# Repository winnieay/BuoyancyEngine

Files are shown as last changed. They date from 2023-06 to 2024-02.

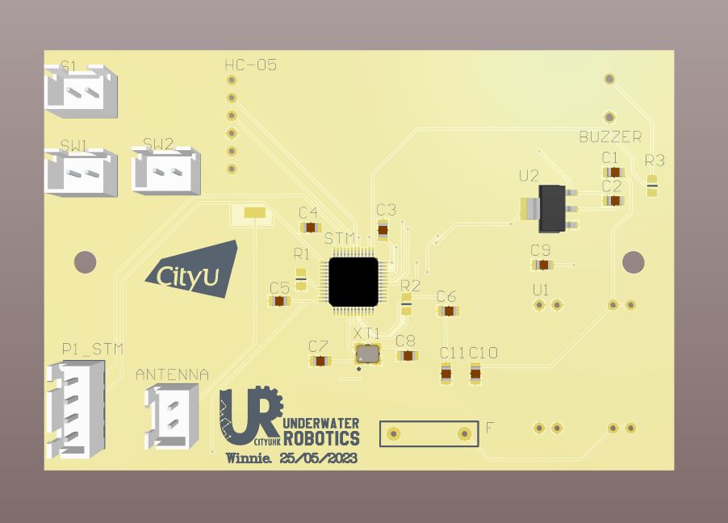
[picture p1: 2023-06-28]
BE_GroundReceiver_PCB/PCB_OUTPUT_3D.JPG

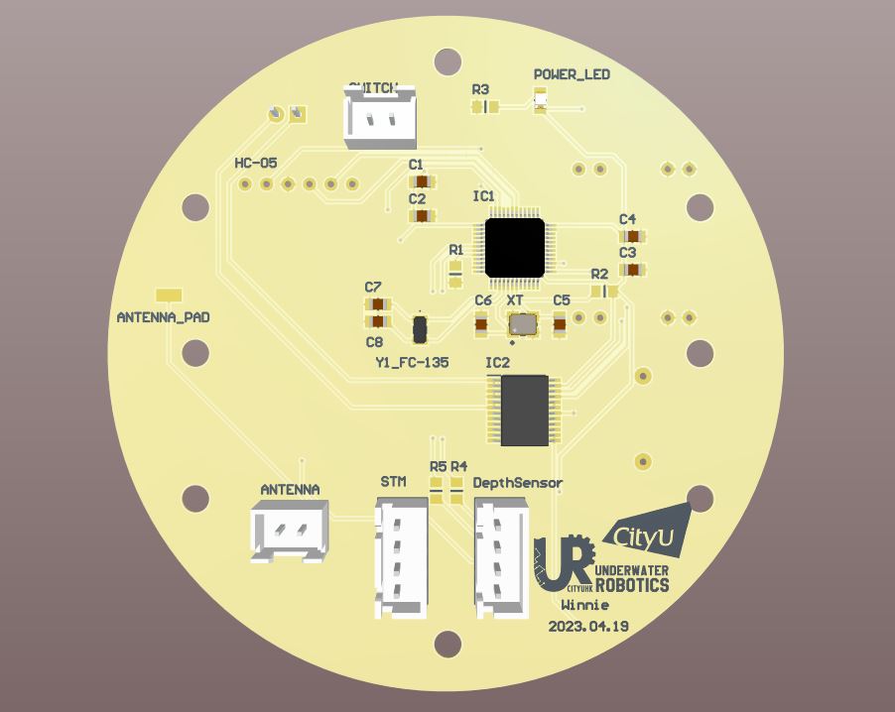
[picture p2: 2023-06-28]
BE_Engine_PCB/PCB_OUTPUT_3D.JPG

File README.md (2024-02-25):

# BuoyancyEngine

The buoyancy engine is built with two watertight enclosures and external mounting support. These two watertight enclosure kits are assembled by PMMA tubes and the aluminum alloy flanges. 

The upper part, the electrical enclosure, includes one 2.4GHz antenna, one customized PCB, one pressure sensor,one peristaltic pump, two 9V batteries and other electrical components. The enclosure on the bottom is mainly used for storing the water drived by the peristaltic pump.

<p align="center">
    <h3>Rendered Buoyancy Engine</h3> <br />
    
    <br />
</p>

<p align="center">
    <h3>Buoyancy Engine Working Example</h3> <br />
   <br />
</p>

<p align="center">
    <h3>PCB Design & Ground Receiver</h3> <br />
   <br />
</p>

<h2>Specification</h2>

1. Watertight Enclosure

+ Thickness: 5mm

+ Outer Dimension: 90mm

+ Length: (Upper)250mm, (Lower)100mm

2. Bouyancy Engine

+ Height: 620mm

+ Dimension: 120mm

<h2>Mechanism</h2>

As peristaltic pumps have no check valves to clog, they excel at driving fluids into lower pressure systems. Therefore, a peristaltic pump would be used to manipulate the motion of the engine: Sinking and Floating. Water is pumped through a flexible silicone tube in a peristaltic motion. Rollers are attached to a rotor that is controlled by a motor. As the rotor turns, the rollers pinch the tubing to force the water through. When the tube is not compressed, the water would be driven into the enclosure or pumped out the enclosure.

To indicate the position of the engine, a pressure sensor is one of the critical components in the engine. The engine could self-identify its position by taking advantage of the relationship between the fluid pressure and depth.

<h2>Data Transmission</h2>

For the communication between the ground station and the engine, a short-range wireless technology standard, Bluetooth, would be used to transmit and receive data. To avoid  improper connection, master-slave mode would be set up in the bluetooth modules. They are only allowed to be paired with each other and keep requiring re-pairing if they disconnect. A 2.4GHz antenna would increase signal strength to guarantee the data transmission even with long distance.

<h2>Buoyancy Support and Mounting Design</h2>

As the engine is positively buoyant, certain weights would be added into the lower enclosure to achieve slight positive buoyancy. Extra weights could be added or mounted to the 3D printed support with zip ties. It provides a flexible approach for buoyancy tuning while the engine is deployed into distinct environments.

To prevent electrical shock, the battery mount is designed to fix the position of the batteries onto the customized PCB. And the customized PCB would be mounting onto the upper aluminum alloy flange.

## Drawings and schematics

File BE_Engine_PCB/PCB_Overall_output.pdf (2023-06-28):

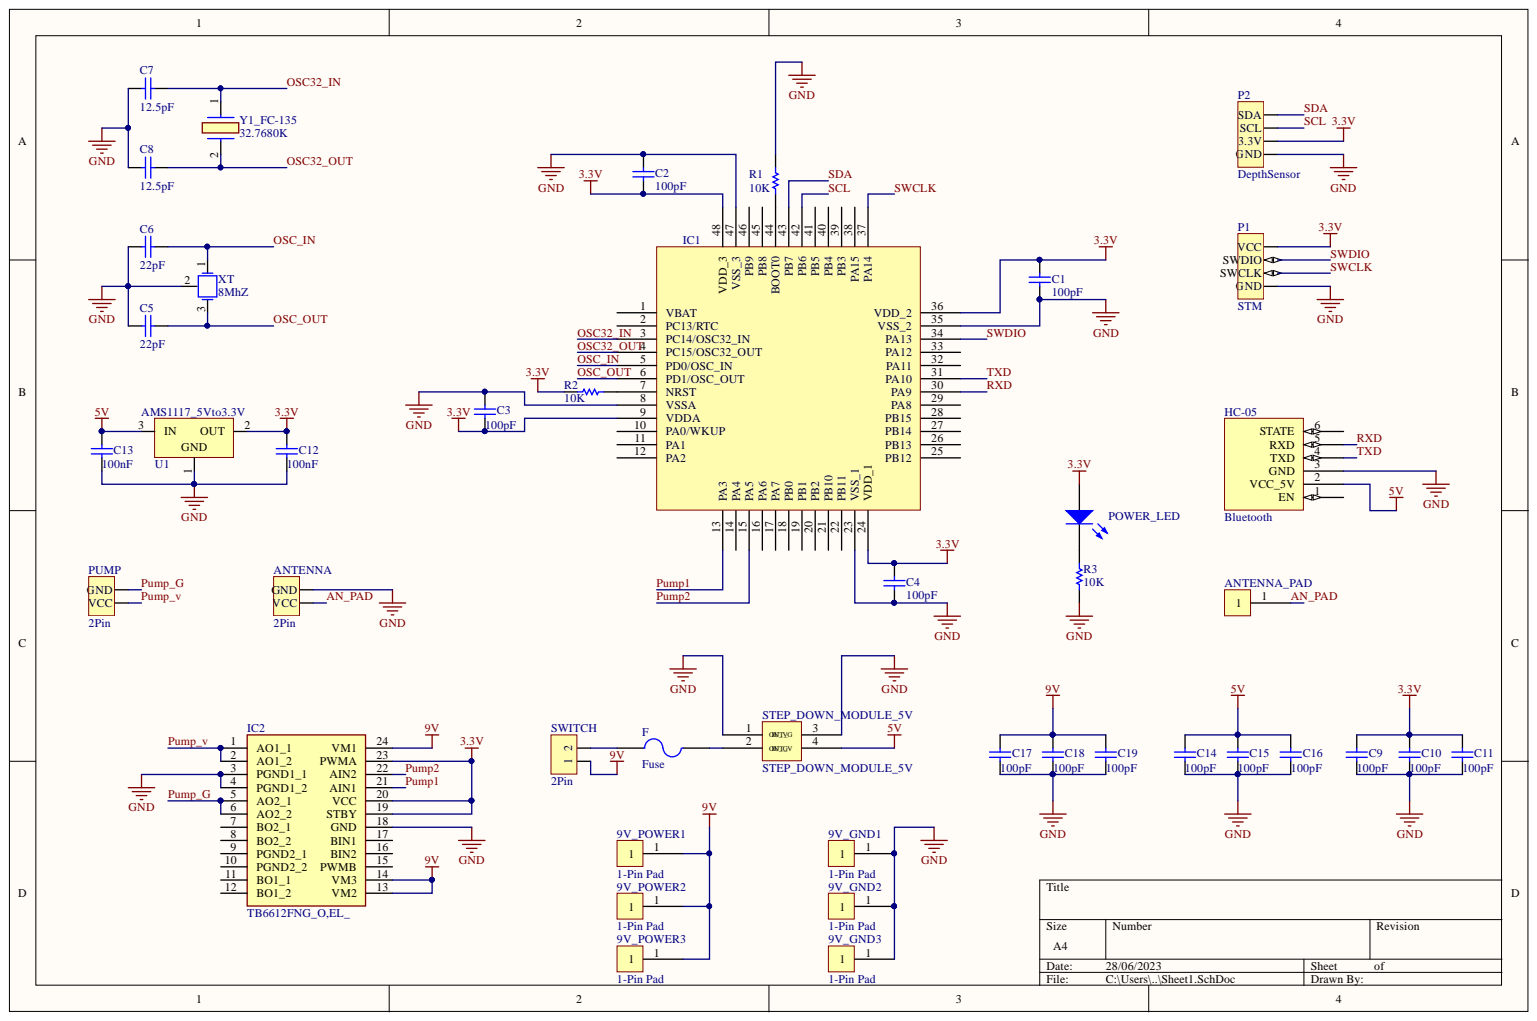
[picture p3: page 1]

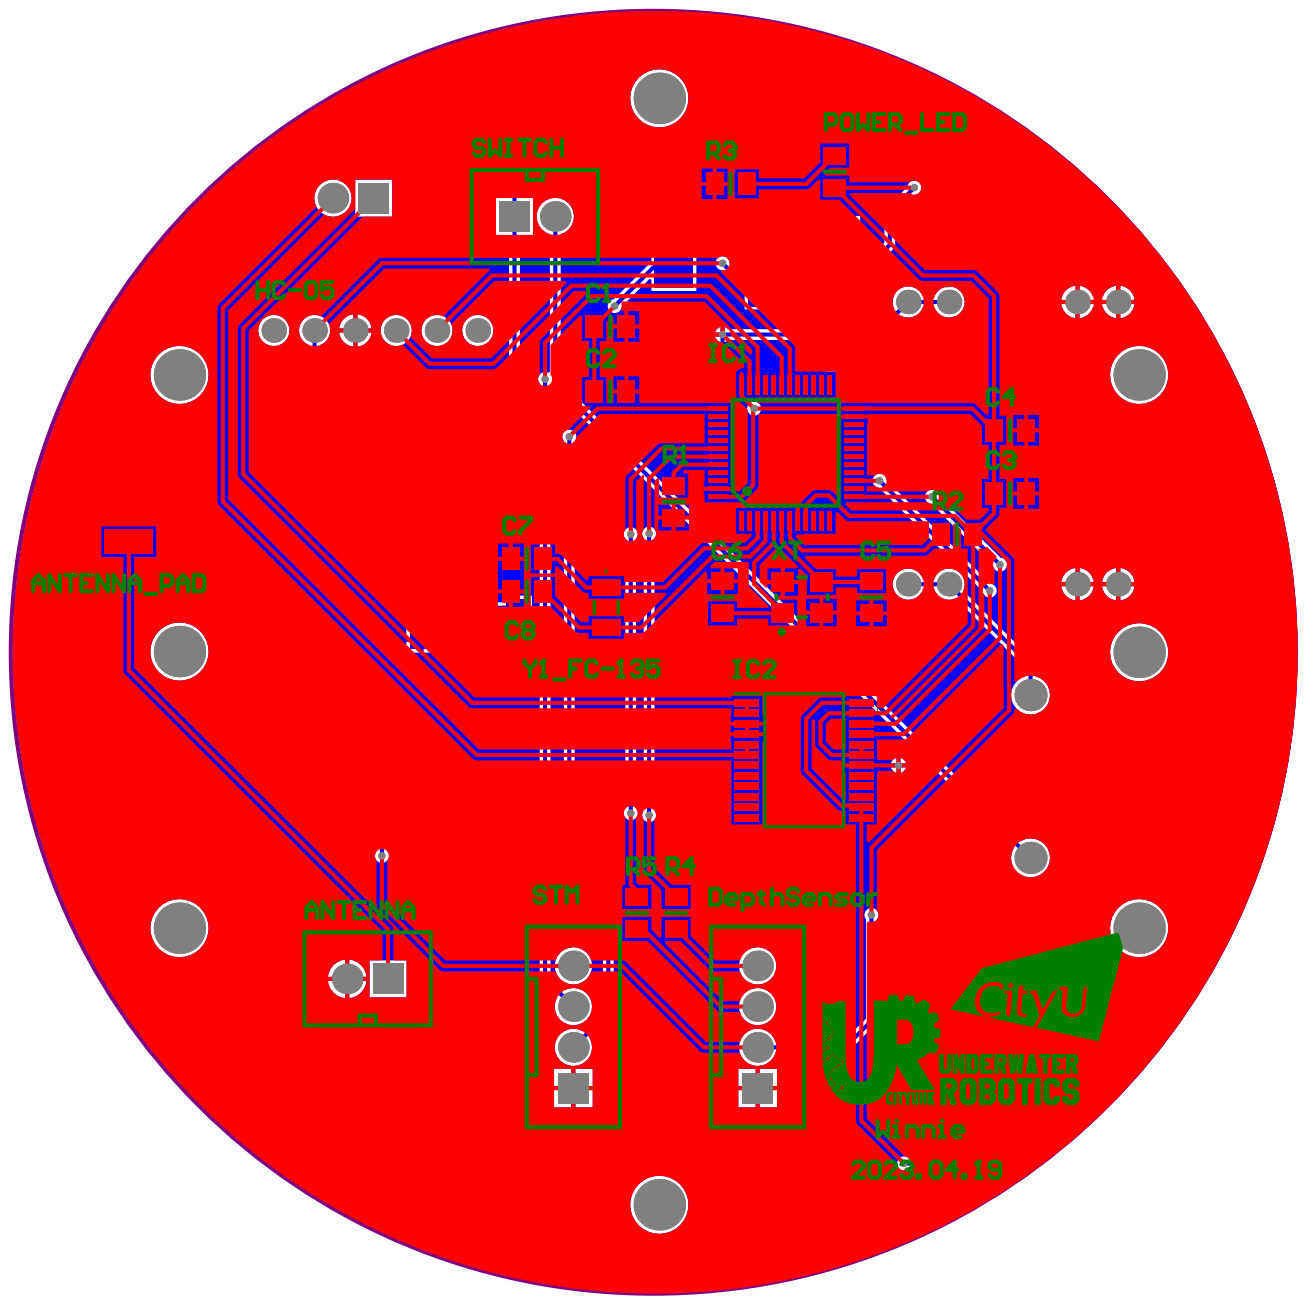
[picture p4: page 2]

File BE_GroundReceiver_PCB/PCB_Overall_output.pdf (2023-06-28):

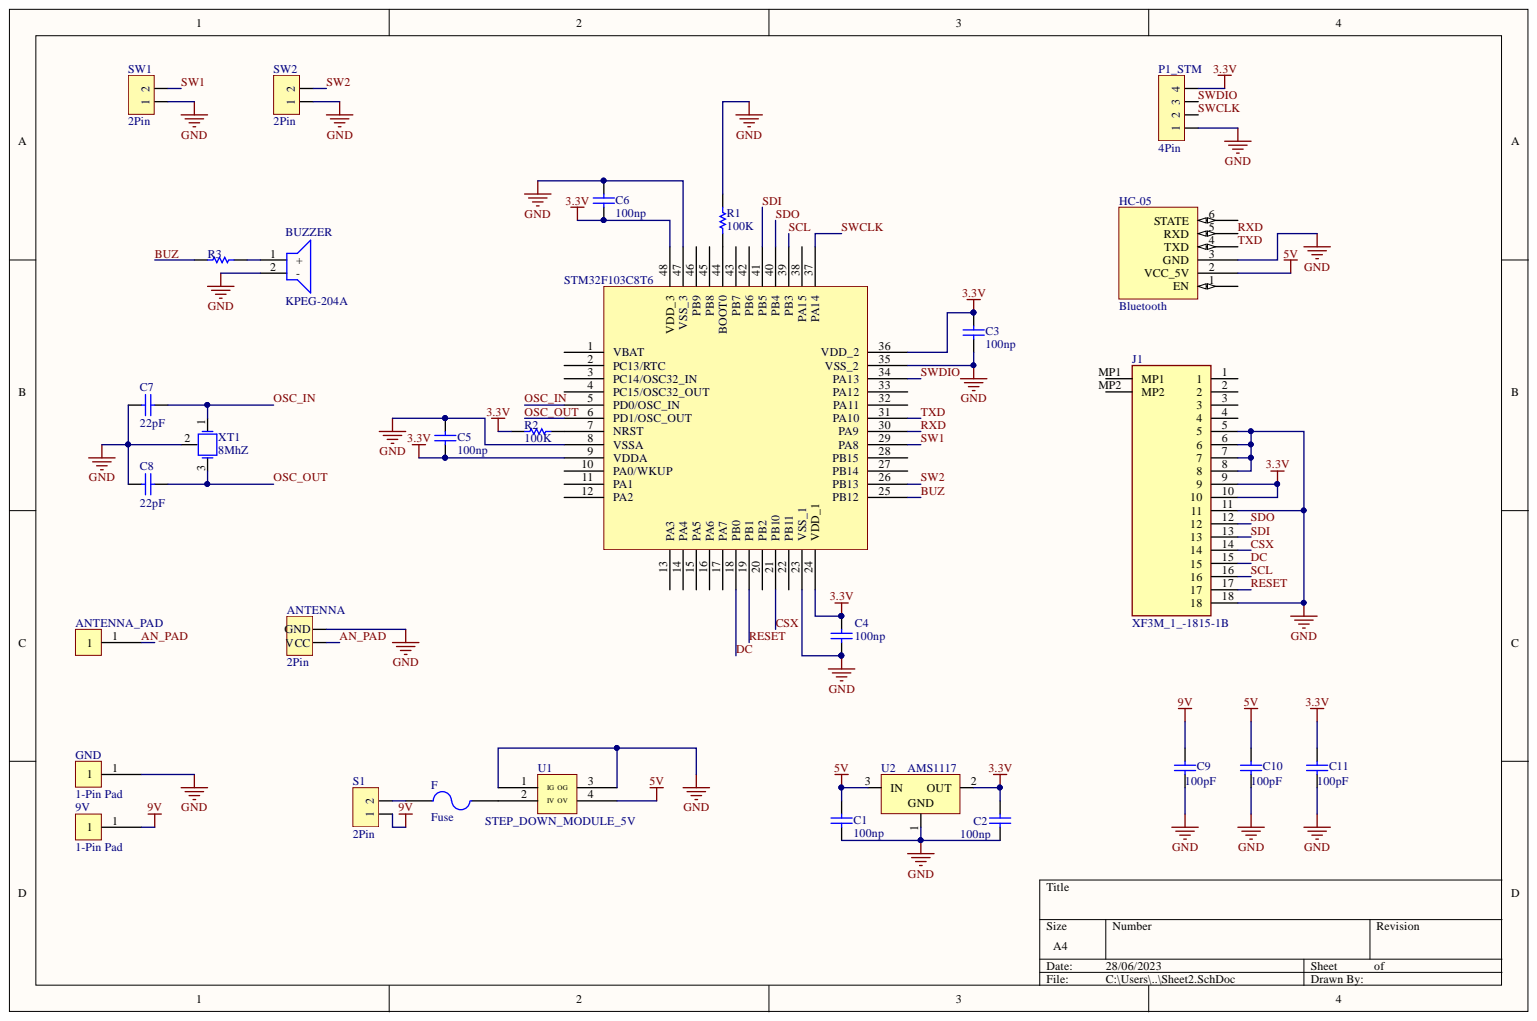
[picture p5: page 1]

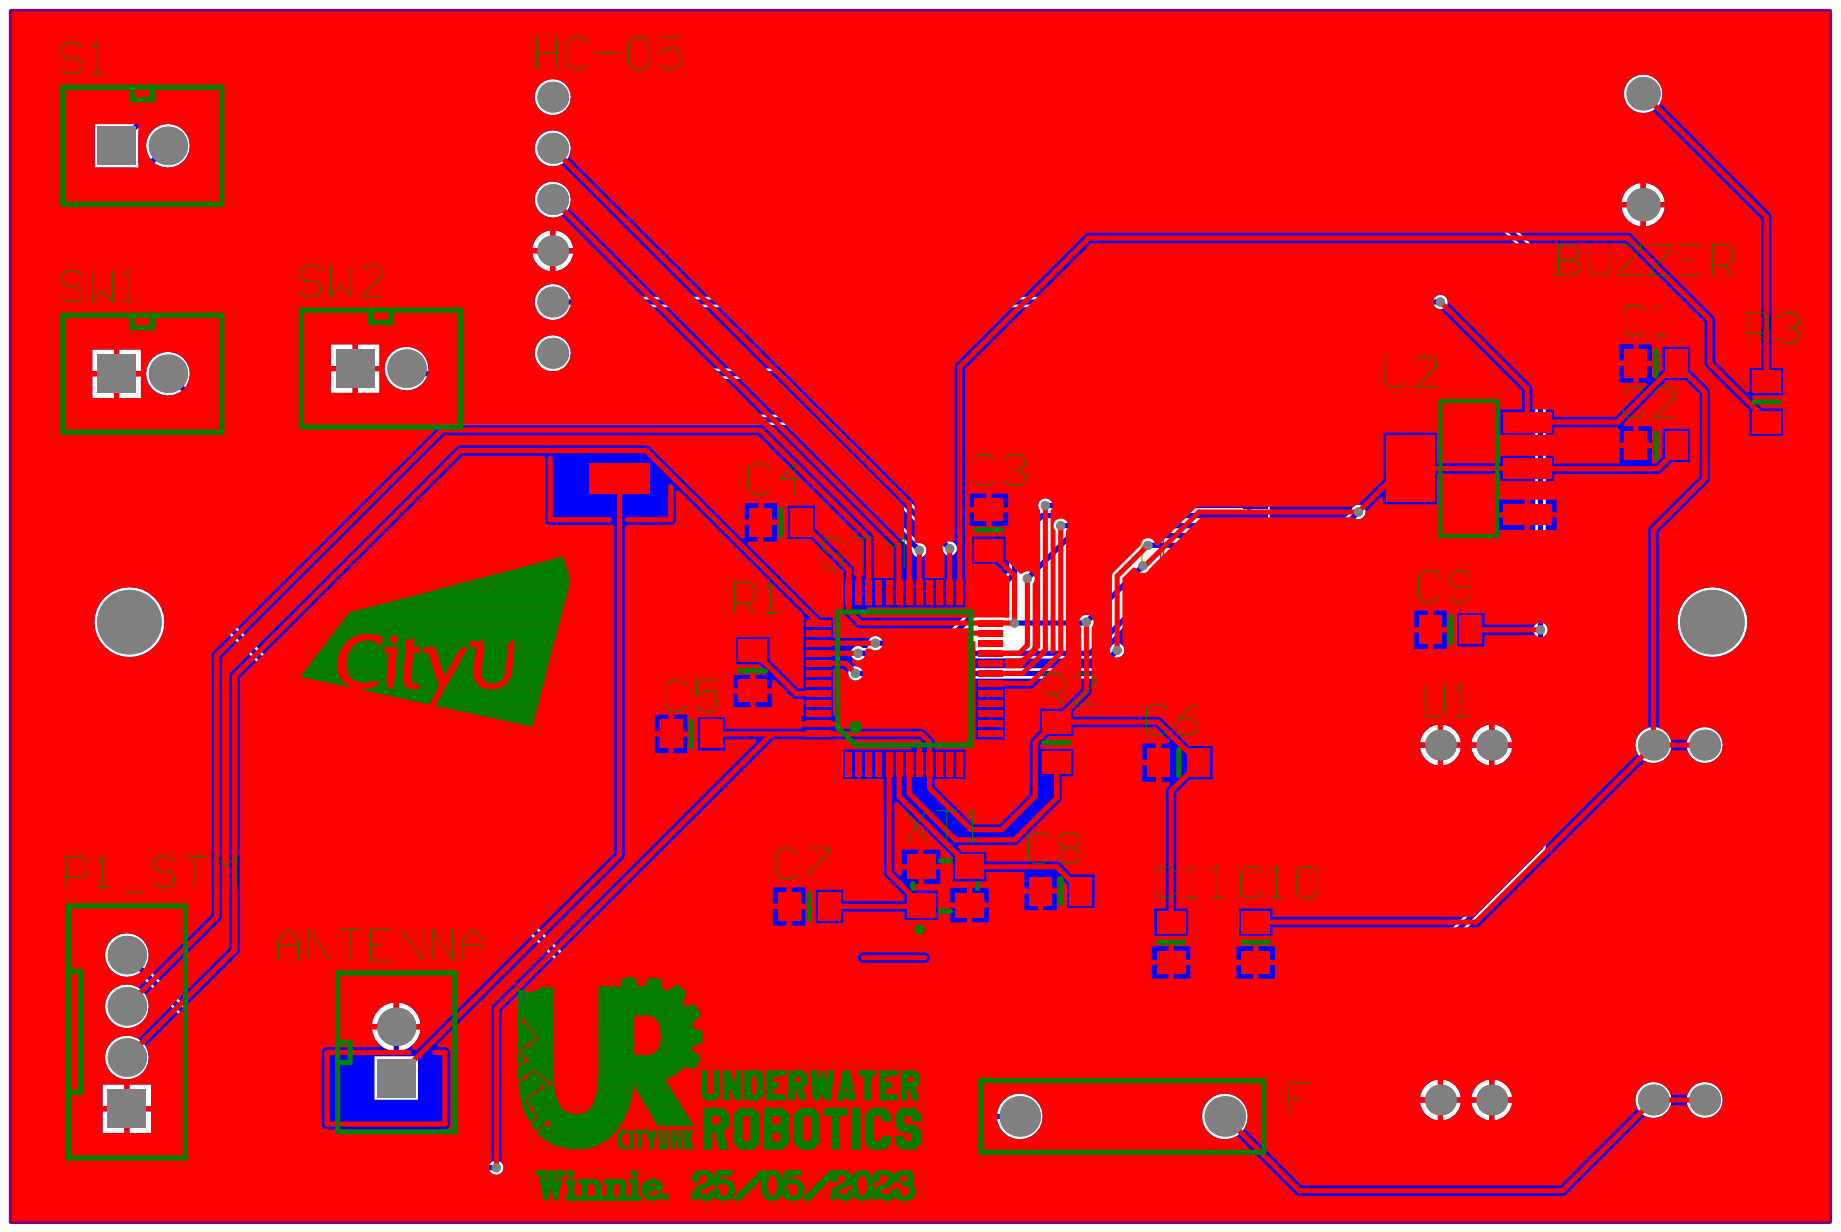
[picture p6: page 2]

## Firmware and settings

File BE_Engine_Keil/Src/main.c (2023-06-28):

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
/* Includes ------------------------------------------------------------------*/
#include "main.h"

/* USER CODE BEGIN Includes */
#include <stdio.h>
#include <string.h>
#include <stdlib.h>



/* USER CODE END Includes */

I2C_HandleTypeDef hi2c1;

RTC_HandleTypeDef hrtc;

TIM_HandleTypeDef htim1;

UART_HandleTypeDef huart1;

/* USER CODE BEGIN PV */
RTC_TimeTypeDef sTime;
RTC_DateTypeDef DateToUpdate;
uint8_t RX_data;
uint8_t TX_BUFFER[7];
uint8_t profileF;
uint8_t i2cadd=0x76<<1;
uint8_t Tsensor;
uint16_t timecounter=950;
uint8_t max=0;
uint16_t c[8];
uint8_t status;
uint8_t command;
uint8_t readresult[2];
char err;
uint32_t conversion;
uint8_t temp[3];

double OFF_;
float Aux;
uint64_t dT, Temperature;
uint64_t SENS;
uint32_t D1_Pres, D2_Temp;		 
uint32_t TEMP2, T2, OFF2, SENS2; 
uint32_t Pressure;			
uint32_t Depth;
float finalPressure;
float finalTemp;
float finalDepth;
uint8_t storeinit=0;


/* USER CODE END PV */

void SystemClock_Config(void);
static void MX_GPIO_Init(void);
static void MX_RTC_Init(void);
static void MX_TIM1_Init(void);
static void MX_USART1_UART_Init(void);
static void MX_I2C1_Init(void);
/* USER CODE BEGIN PFP */
void sinking();
void floating();
void resetoff();
void SensorReset();
unsigned char crc4(unsigned int n_prom[]) ;
void SensorGetCvalues();
void SensorGetConversion(uint8_t command);
void SensorGetData();
void AskForConnection();
void ProfileRun();


/* USER CODE END PFP */

/**
  * @brief  The application entry point.
  * @retval int
  */
int main(void)
{
  /* MCU Configuration--------------------------------------------------------*/

  /* Reset of all peripherals, Initializes the Flash interface and the Systick. */
  HAL_Init();

  /* Configure the system clock */
  SystemClock_Config();

  /* Initialize all configured peripherals */
  MX_GPIO_Init();
  MX_RTC_Init();
  MX_TIM1_Init();
  MX_USART1_UART_Init();
  MX_I2C1_Init();
  /* USER CODE BEGIN 2 */
	
	

	
	resetoff();
	
	
//reset pressure sensor
	//SensorReset();
	
//checking whether pressure sensor is ready
	//if(HAL_I2C_IsDeviceReady (&hi2c1, i2cadd, 10, HAL_MAX_DELAY)==HAL_OK)status=1;
	//HAL_Delay(10);
	//HAL_Delay(40);
	/*c1-c6:
	Pressure sensitivity, Pressure offset, 
	Temperature coefficient of pressure sensitivity,Temperature coefficient of pressure offset,
	Reference temperature, Temperature coefficient of the temperature */
	//SensorGetCvalues();
	HAL_Delay(40);
	HAL_UART_Receive_IT(&huart1, &RX_data, 1);

  /* USER CODE END 2 */

  /* Infinite loop */
  /* USER CODE BEGIN WHILE */
  while (1)
  {

		HAL_RTC_GetTime(&hrtc,&sTime,RTC_FORMAT_BIN);
		HAL_RTC_GetDate(&hrtc,&DateToUpdate,RTC_FORMAT_BIN);
		TX_BUFFER[0]=sTime.Hours;
		TX_BUFFER[1]=sTime.Minutes;
		TX_BUFFER[2]=sTime.Seconds;
		TX_BUFFER[3]=DateToUpdate.Year;
		TX_BUFFER[4]=DateToUpdate.Month;
		TX_BUFFER[5]=DateToUpdate.Date;
		TX_BUFFER[6]=0xff;
		
		
		//measure pressure each two seconds 
		//SensorGetData();
		//TX_BUFFER[7]=finalDepth;
		HAL_UART_Transmit(&huart1, TX_BUFFER, 7, 100);
		
			HAL_Delay(100);
			timecounter++;
			
			if(timecounter==450)
					resetoff();
			if(timecounter==460)
				 floating();
			
			if(timecounter==970){
				resetoff();
				timecounter=980;
			}
			
			if(timecounter==1000)
				timecounter=980;


//				//if(finalDepth==storeinit+500*3)
//				if(finalDepth==storeinit+150)
//					floating();
//				if(finalDepth==storeinit+10||finalDepth==storeinit-15)
//					resetoff();

		
  }
    /* USER CODE END WHILE */

}

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
/* USER CODE BEGIN 4 */

void HAL_UART_RxCpltCallback(UART_HandleTypeDef *huart)  
{
	 if(RX_data==77||RX_data==66){
		 timecounter=0;
		ProfileRun();
	 }
		 
	if(RX_data==80||RX_data==88)
		 resetoff();
	 
	 HAL_UART_Receive_IT(&huart1, &RX_data, 1);
	 
}
void ProfileRun(){
		sinking();
		
		
}
unsigned char crc4(unsigned int n_prom[]) // n_prom defined as 8x unsigned int (n_prom[8])
{
	int cnt; // simple counter
	unsigned int n_rem=0; // crc remainder
	unsigned char n_bit;
	n_prom[0]=((n_prom[0]) & 0x0FFF); // CRC byte is replaced by 0
	n_prom[7]=0; // Subsidiary value, set to 0
	for (cnt = 0; cnt < 16; cnt++) // operation is performed on bytes
	 { // choose LSB or MSB
	 if (cnt%2==1) n_rem ^= (unsigned short) ((n_prom[cnt>>1]) & 0x00FF);
	 else n_rem ^= (unsigned short) (n_prom[cnt>>1]>>8);
	 for (n_bit = 8; n_bit > 0; n_bit--)
	 {
	 if (n_rem & (0x8000)) n_rem = (n_rem << 1) ^ 0x3000;
	 else n_rem = (n_rem << 1);
	 }
	 }
	n_rem= ((n_rem >> 12) & 0x000F); // final 4-bit remainder is CRC code
	return (n_rem ^ 0x00);
}
void sinking(){
	HAL_GPIO_WritePin(GPIOA, GPIO_PIN_3, 1);
	HAL_GPIO_WritePin(GPIOA, GPIO_PIN_5, 0);
}
void floating(){
	HAL_GPIO_WritePin(GPIOA, GPIO_PIN_3, 0);
	HAL_GPIO_WritePin(GPIOA, GPIO_PIN_5, 1);
}
void resetoff(){
	HAL_GPIO_WritePin(GPIOA, GPIO_PIN_3, 0);
	HAL_GPIO_WritePin(GPIOA, GPIO_PIN_5, 0);
}
void SensorReset(){
	command=0x1E;
	HAL_I2C_Master_Transmit(&hi2c1, (i2cadd), &command, 1, HAL_MAX_DELAY);
	HAL_Delay(20);
}
//c1-c6:
//Pressure sensitivity, Pressure offset, 
//Temperature coefficient of pressure sensitivity,Temperature coefficient of pressure offset,
//Reference temperature, Temperature coefficient of the temperature 
void SensorGetCvalues(){
	
	for(uint8_t i=0;i<7;i++){
		command=0xA0+i*2;
		//command=0xA0+i<<1);
		//HAL_Delay(20);
		HAL_I2C_Master_Transmit(&hi2c1, (i2cadd), &command, 1, HAL_MAX_DELAY);
		HAL_Delay(20);
		HAL_I2C_Master_Receive(&hi2c1, (i2cadd), readresult,2,100);
		
		
	HAL_Delay(20);
//		HAL_I2C_Master_Receive(&hi2c1, (i2cadd), readresult,1,100);
//		command=0xA0+i*2+2;
//		HAL_Delay(20);
//		HAL_I2C_Master_Transmit(&hi2c1, (i2cadd), &command, 1, HAL_MAX_DELAY);
//		HAL_Delay(20);
//		HAL_I2C_Master_Receive(&hi2c1, (i2cadd), &readresult[1],1,100);
//  	HAL_Delay(20);
		c[i] = (((uint16_t)readresult[1] << 8) | readresult[0]);
		
		//c[i]=readresult;
	}
	
	err=crc4((unsigned int*)c);
}

void SensorGetConversion(uint8_t command){

	
	HAL_I2C_Master_Transmit(&hi2c1, (i2cadd), &command, 1, HAL_MAX_DELAY);
	HAL_Delay(20);	
	command=0x00;
	HAL_I2C_Master_Transmit(&hi2c1, (i2cadd), &command, 1, HAL_MAX_DELAY);
	HAL_Delay(20);
	HAL_I2C_Master_Receive(&hi2c1, (i2cadd), temp,3,100);
	conversion = ((uint32_t)temp[0] << 16) | ((uint32_t)temp[1] << 8) | temp[2];
	
}

void SensorGetData(){
	
	SensorGetConversion(0x46);
	D1_Pres=conversion;
	HAL_Delay(20);
	SensorGetConversion(0x56);
	D2_Temp=conversion;

	if (D2_Temp > (((uint32_t)c[4]) * 256.0))
	{
		dT = D2_Temp - (((uint32_t)c[6]) * 256);
		Temperature = 2000.0 + dT * ((uint32_t)c[6]) / 8388608.0f;
		OFF_ = (uint32_t)c[2] * 65536.0f + ((uint32_t)c[4] * dT) / 128.0f;
		SENS = (uint32_t)c[1] * 32768.0f + ((uint32_t)c[3] * dT) / 256.0f;
	}
	else
	{
		dT = (((uint32_t)c[5]) * 256.0f) - D2_Temp;
		Temperature = 2000.0f + dT * ((uint32_t)c[6]) / 8388608.0f;
		OFF_ = (uint32_t)c[2] * 65536.0f - ((uint32_t)c[4] * dT) / 128.0;
		SENS = (uint32_t)c[1] * 32768.0f - ((uint32_t)c[3] * dT) / 256.0;
	}
	
	if (Temperature < 2000) // low temp
	{
		Aux = (2000.0 - Temperature) * (2000.0 - Temperature);
		T2 = 3.0 * (dT * dT) / 8589934592.0f;
		OFF2 = 3 * Aux / 2;
		SENS2 = 5 * Aux / 8;
	}
	else
	{
		Aux = (Temperature - 2000) * (Temperature - 2000);
		T2 = 2 * (dT * dT) / 137438953472.0f;
		OFF2 = 1 * Aux / 16;
		SENS2 = 0;
	}
	OFF_ = OFF_ - OFF2;
	SENS = SENS - SENS2;
	
	finalTemp = (float)(Temperature - T2) / 100.0f;
	finalPressure =(float)((D1_Pres * SENS / 2097152.0f - OFF_) / 8192.0f) / 10.0f;
	//finalDepth = 0-(0.986923267* ( (0.0f-finalPressure-1013.25)*0.001))/10;
	finalDepth=0.986923267f*(finalPressure-985.0f);
	
	if(storeinit==0){
		storeinit=finalPressure;
	}
}

void AskForConnection(){
	profileF=88;
	while(1){
		HAL_UART_Transmit(&huart1, &profileF, 1, 100);
		HAL_Delay(500);
		if(RX_data==88){
			RX_data=0;
			break;
		}
	}
}

/* USER CODE END 4 */
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


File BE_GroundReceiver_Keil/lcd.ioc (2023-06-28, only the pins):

Mcu.UserName=STM32F103C8Tx
PA10.Signal=USART1_RX
PA13.Signal=SYS_JTMS-SWDIO
PA14.Signal=SYS_JTCK-SWCLK
PA7.Signal=GPIO_Input
PA8.Signal=GPIO_Input
PA9.Signal=USART1_TX
PB0.Signal=GPIO_Output
PB1.Signal=GPIO_Output
PB10.Signal=GPIO_Output
PB15.Signal=GPIO_Output
PB2.Signal=GPIO_Output
PB3.Signal=SPI1_SCK
PB4.Signal=SPI1_MISO
PB5.Signal=SPI1_MOSI
PD0-OSC_IN.Signal=RCC_OSC_IN
PD1-OSC_OUT.Signal=RCC_OSC_OUT

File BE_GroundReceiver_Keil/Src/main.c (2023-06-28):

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
/* Includes ------------------------------------------------------------------*/
#include "main.h"

/* USER CODE BEGIN Includes */
#include <stdio.h>
#include <string.h>
#include <stdlib.h>
#include <stdbool.h>



/* USER CODE END Includes */

/* USER CODE BEGIN PD */



#define CSX_PORT GPIOB
#define CSX_PIN GPIO_PIN_10

#define DC_PORT GPIOB
#define DC_PIN GPIO_PIN_0

#define RESET_PORT GPIOB
#define RESET_PIN GPIO_PIN_1


#define LCD_REST_LOW()   HAL_GPIO_WritePin(RESET_PORT, RESET_PIN, 0)
#define LCD_REST_HIGH()  HAL_GPIO_WritePin(RESET_PORT, RESET_PIN, 1)

#define LCD_DC_LOW()     HAL_GPIO_WritePin(DC_PORT, DC_PIN, 0)
#define LCD_DC_HIGH()    HAL_GPIO_WritePin(DC_PORT, DC_PIN, 1)

#define LCD_CS_LOW()     HAL_GPIO_WritePin(CSX_PORT, CSX_PIN, 0)
#define LCD_CS_HIGH()    HAL_GPIO_WritePin(CSX_PORT, CSX_PIN, 1)

const unsigned char ascii_3216[][64]={
{0x00,0x00,0x00,0x00,0x00,0x00,0x00,0x00,0x00,0x00,0x00,0x00,0x00,0x00,0x00,0x00,0x00,0x00,0x00,0x00,0x00,0x00,0x00,0x00,0x00,0x00,0x00,0x00,0x00,0x00,0x00,0x00,0x00,0x00,0x00,0x00,0x00,0x00,0x00,0x00,0x00,0x00,0x00,0x00,0x00,0x00,0x00,0x00,0x00,0x00,0x00,0x00,0x00,0x00,0x00,0x00,0x00,0x00,0x00,0x00,0x00,0x00,0x00,0x00},/*" ",0*/
{0x00,0x00,0x00,0x00,0x00,0x00,0x00,0x00,0x00,0x00,0xC0,0x01,0xC0,0x01,0xC0,0x01,0xC0,0x01,0xC0,0x01,0xC0,0x01,0xC0,0x01,0x80,0x00,0x80,0x00,0x80,0x00,0x80,0x00,0x80,0x00,0x80,0x00,0x80,0x00,0x00,0x00,0x00,0x00,0x00,0x00,0x00,0x00,0x80,0x01,0xC0,0x03,0xC0,0x03,0x80,0x01,0x00,0x00,0x00,0x00,0x00,0x00,0x00,0x00,0x00,0x00},/*"!",1*/
{0x00,0x00,0x00,0x00,0x00,0x00,0xE0,0x1C,0xE0,0x1C,0xF0,0x1E,0x70,0x0E,0x38,0x07,0x18,0x03,0x08,0x01,0x84,0x00,0x00,0x00,0x00,0x00,0x00,0x00,0x00,0x00,0x00,0x00,0x00,0x00,0x00,0x00,0x00,0x00,0x00,0x00,0x00,0x00,0x00,0x00,0x00,0x00,0x00,0x00,0x00,0x00,0x00,0x00,0x00,0x00,0x00,0x00,0x00,0x00,0x00,0x00,0x00,0x00,0x00,0x00},/*""",2*/
{0x00,0x00,0x00,0x00,0x00,0x00,0x00,0x00,0x00,0x00,0x00,0x00,0x20,0x10,0x20,0x10,0x20,0x10,0x20,0x10,0x20,0x10,0xFE,0x7F,0xFE,0x7F,0x10,0x08,0x10,0x08,0x10,0x08,0x10,0x08,0x10,0x08,0x10,0x08,0x10,0x08,0xFE,0x7F,0xFE,0x7F,0x08,0x04,0x08,0x04,0x08,0x04,0x08,0x04,0x08,0x04,0x00,0x00,0x00,0x00,0x00,0x00,0x00,0x00,0x00,0x00},/*"#",3*/
{0x00,0x00,0x00,0x00,0x00,0x00,0x00,0x00,0x00,0x01,0x00,0x01,0xC0,0x07,0x60,0x19,0x10,0x31,0x18,0x31,0x18,0x39,0x18,0x39,0x38,0x01,0x70,0x01,0xE0,0x01,0xC0,0x03,0x80,0x07,0x00,0x0F,0x00,0x1D,0x00,0x39,0x00,0x31,0x1C,0x31,0x1C,0x31,0x0C,0x31,0x0C,0x11,0x18,0x0D,0xE0,0x07,0x00,0x01,0x00,0x01,0x00,0x01,0x00,0x00,0x00,0x00},/*"$",4*/
{0x00,0x00,0x00,0x00,0x00,0x00,0x00,0x00,0x00,0x00,0x00,0x00,0x1C,0x10,0x36,0x18,0x63,0x08,0x63,0x0C,0x63,0x04,0x63,0x04,0x63,0x02,0x63,0x02,0x63,0x01,0x36,0x1D,0x9C,0x37,0x80,0x22,0x80,0x63,0x40,0x63,0x40,0x63,0x20,0x63,0x20,0x63,0x30,0x63,0x10,0x22,0x18,0x36,0x08,0x1C,0x00,0x00,0x00,0x00,0x00,0x00,0x00,0x00,0x00,0x00},/*"%",5*/
{0x00,0x00,0x00,0x00,0x00,0x00,0x00,0x00,0x00,0x00,0x00,0x00,0xF0,0x00,0x98,0x01,0x8C,0x01,0x8C,0x01,0x8C,0x01,0x8C,0x01,0x8C,0x00,0xCC,0x00,0x78,0x00,0x18,0x3E,0x1C,0x08,0x36,0x08,0x32,0x08,0x63,0x04,0x63,0x04,0xC3,0x04,0xC3,0x03,0x83,0x43,0x06,0x43,0x8E,0x26,0x78,0x1C,0x00,0x00,0x00,0x00,0x00,0x00,0x00,0x00,0x00,0x00},/*"&",6*/
{0x00,0x00,0x00,0x00,0x00,0x00,0x1C,0x00,0x3C,0x00,0x3C,0x00,0x30,0x00,0x30,0x00,0x10,0x00,0x0C,0x00,0x06,0x00,0x00,0x00,0x00,0x00,0x00,0x00,0x00,0x00,0x00,0x00,0x00,0x00,0x00,0x00,0x00,0x00,0x00,0x00,0x00,0x00,0x00,0x00,0x00,0x00,0x00,0x00,0x00,0x00,0x00,0x00,0x00,0x00,0x00,0x00,0x00,0x00,0x00,0x00,0x00,0x00,0x00,0x00},/*"'",7*/
{0x00,0x00,0x00,0x00,0x00,0x00,0x00,0x40,0x00,0x20,0x00,0x10,0x00,0x08,0x00,0x0C,0x00,0x04,0x00,0x06,0x00,0x03,0x00,0x03,0x00,0x03,0x80,0x01,0x80,0x01,0x80,0x01,0x80,0x01,0x80,0x01,0x80,0x01,0x80,0x01,0x80,0x01,0x00,0x03,0x00,0x03,0x00,0x03,0x00,0x06,0x00,0x06,0x00,0x0C,0x00,0x08,0x00,0x10,0x00,0x20,0x00,0x40,0x00,0x00},/*"(",8*/
{0x00,0x00,0x00,0x00,0x00,0x00,0x02,0x00,0x04,0x00,0x08,0x00,0x10,0x00,0x30,0x00,0x20,0x00,0x60,0x00,0xC0,0x00,0xC0,0x00,0xC0,0x00,0x80,0x01,0x80,0x01,0x80,0x01,0x80,0x01,0x80,0x01,0x80,0x01,0x80,0x01,0x80,0x01,0xC0,0x00,0xC0,0x00,0xC0,0x00,0x60,0x00,0x60,0x00,0x30,0x00,0x10,0x00,0x08,0x00,0x04,0x00,0x02,0x00,0x00,0x00},/*")",9*/
{0x00,0x00,0x00,0x00,0x00,0x00,0x00,0x00,0x00,0x00,0x00,0x00,0x00,0x00,0x00,0x00,0x00,0x01,0x80,0x03,0x80,0x03,0x00,0x01,0x1C,0x71,0x3C,0x79,0x78,0x3D,0xC0,0x07,0x00,0x01,0xC0,0x07,0x78,0x3D,0x3C,0x79,0x1C,0x71,0x00,0x01,0x80,0x03,0x80,0x03,0x80,0x01,0x00,0x00,0x00,0x00,0x00,0x00,0x00,0x00,0x00,0x00,0x00,0x00,0x00,0x00},/*"*",10*/
{0x00,0x00,0x00,0x00,0x00,0x00,0x00,0x00,0x00,0x00,0x00,0x00,0x00,0x00,0x00,0x00,0x00,0x00,0x00,0x01,0x00,0x01,0x00,0x01,0x00,0x01,0x00,0x01,0x00,0x01,0x00,0x01,0xFC,0x7F,0x00,0x01,0x00,0x01,0x00,0x01,0x00,0x01,0x00,0x01,0x00,0x01,0x00,0x01,0x00,0x00,0x00,0x00,0x00,0x00,0x00,0x00,0x00,0x00,0x00,0x00,0x00,0x00,0x00,0x00},/*"+",11*/
{0x00,0x00,0x00,0x00,0x00,0x00,0x00,0x00,0x00,0x00,0x00,0x00,0x00,0x00,0x00,0x00,0x00,0x00,0x00,0x00,0x00,0x00,0x00,0x00,0x00,0x00,0x00,0x00,0x00,0x00,0x00,0x00,0x00,0x00,0x00,0x00,0x00,0x00,0x00,0x00,0x00,0x00,0x00,0x00,0x00,0x00,0x00,0x00,0x1C,0x00,0x3C,0x00,0x3C,0x00,0x30,0x00,0x30,0x00,0x10,0x00,0x0C,0x00,0x06,0x00},/*",",12*/
{0x00,0x00,0x00,0x00,0x00,0x00,0x00,0x00,0x00,0x00,0x00,0x00,0x00,0x00,0x00,0x00,0x00,0x00,0x00,0x00,0x00,0x00,0x00,0x00,0x00,0x00,0x00,0x00,0x00,0x00,0x00,0x00,0xFE,0x7F,0x00,0x00,0x00,0x00,0x00,0x00,0x00,0x00,0x00,0x00,0x00,0x00,0x00,0x00,0x00,0x00,0x00,0x00,0x00,0x00,0x00,0x00,0x00,0x00,0x00,0x00,0x00,0x00,0x00,0x00},/*"-",13*/
{0x00,0x00,0x00,0x00,0x00,0x00,0x00,0x00,0x00,0x00,0x00,0x00,0x00,0x00,0x00,0x00,0x00,0x00,0x00,0x00,0x00,0x00,0x00,0x00,0x00,0x00,0x00,0x00,0x00,0x00,0x00,0x00,0x00,0x00,0x00,0x00,0x00,0x00,0x00,0x00,0x00,0x00,0x00,0x00,0x00,0x00,0x18,0x00,0x3C,0x00,0x3C,0x00,0x18,0x00,0x00,0x00,0x00,0x00,0x00,0x00,0x00,0x00,0x00,0x00},/*".",14*/
{0x00,0x00,0x00,0x00,0x00,0x00,0x00,0x40,0x00,0x60,0x00,0x20,0x00,0x30,0x00,0x10,0x00,0x18,0x00,0x08,0x00,0x0C,0x00,0x04,0x00,0x06,0x00,0x02,0x00,0x03,0x00,0x01,0x80,0x01,0x80,0x00,0xC0,0x00,0x40,0x00,0x60,0x00,0x20,0x00,0x30,0x00,0x10,0x00,0x18,0x00,0x08,0x00,0x0C,0x00,0x04,0x00,0x06,0x00,0x02,0x00,0x00,0x00,0x00,0x00},/*"/",15*/
{0x00,0x00,0x00,0x00,0x00,0x00,0x00,0x00,0x00,0x00,0x00,0x00,0xC0,0x07,0x60,0x0C,0x30,0x18,0x18,0x30,0x18,0x30,0x18,0x20,0x0C,0x60,0x0C,0x60,0x0C,0x60,0x0C,0x60,0x0C,0x60,0x0C,0x60,0x0C,0x60,0x0C,0x60,0x0C,0x60,0x18,0x20,0x18,0x30,0x18,0x30,0x30,0x18,0x60,0x0C,0xC0,0x07,0x00,0x00,0x00,0x00,0x00,0x00,0x00,0x00,0x00,0x00},/*"0",16*/
{0x00,0x00,0x00,0x00,0x00,0x00,0x00,0x00,0x00,0x00,0x00,0x00,0x00,0x01,0x80,0x01,0xF8,0x01,0x80,0x01,0x80,0x01,0x80,0x01,0x80,0x01,0x80,0x01,0x80,0x01,0x80,0x01,0x80,0x01,0x80,0x01,0x80,0x01,0x80,0x01,0x80,0x01,0x80,0x01,0x80,0x01,0x80,0x01,0x80,0x01,0xC0,0x03,0xF8,0x1F,0x00,0x00,0x00,0x00,0x00,0x00,0x00,0x00,0x00,0x00},/*"1",17*/
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

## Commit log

2023-06-28 all files
    [PCB1.GBL, PCB1.GBO, PCB1.GBP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]
2023-06-28 generate the pcb output to pdf
    [PCB_Project1.PrjPCB, PCB_Project2.PrjPCB]

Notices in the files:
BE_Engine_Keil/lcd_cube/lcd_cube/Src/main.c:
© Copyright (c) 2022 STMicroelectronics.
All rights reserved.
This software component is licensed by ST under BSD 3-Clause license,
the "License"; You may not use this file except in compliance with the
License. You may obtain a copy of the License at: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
